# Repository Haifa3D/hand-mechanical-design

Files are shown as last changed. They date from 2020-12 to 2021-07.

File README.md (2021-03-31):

# Oded Hand Mechanical Design  

This project is a sub-project of Haifa3D Robotic Hand.
In this project, we present the mechanical design of the Oded Hand – a 3D printed robotic hand with five micro-DC motors. 
The aim of this design is to be low cost, accessible, easy to assemble, robust and lightweight.  

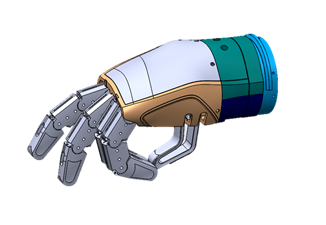
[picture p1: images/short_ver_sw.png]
diagram
   hand_gif  

## Design Description  
The Oded Hand can perform a variety of user-defined hand configurations using an autonomous adaptive grip along with a variety of grip force levels.
The mechanical design consists of four fingers with four different tendon-driven mechanisms actuated by four different micro-DC motors, a passive thumb with two discrete positions using two magnets and wrist rotation driven by planetary gears and a DC motor. 
Each finger is an independent module, hence from a developer point-of-view, you can check new finger designs and change the number of fingers in your hand model. For more details, see the [project presentation](docs/project_presentation.pdf)
All five independent micro-DC motors are driven by a microcontroller system which measures the motors’ current state (see our [Electronic Design](https://github.com/Haifa3D/hand-electronic-design)) and communicate via Bluetooth with additional sensors or systems (see our [Mobile App](https://github.com/Haifa3D/haifa3d-hand-app)).  

## Who can benefit from this Design?  
The design is suitable for users with a below elbow amputation.
We welcome any new developers to enhance our design or to use the Oded Hand as a simulator for your new sensors/algorithms/methods that would potentially help users to control their prosthetic hand.

## Design Files and Versions  
See our detailed [Manual](docs/manual_05dec20.pdf), including printing parameters, assembly instruction and images. *Notice: some of the images are from our previous version but the current version assembly and functionality can be deduced easily according to the same instructions.*
The STL files can be found [here](stl_files) as a folder or [here](stl_files.zip) as a zip file ready to download. The source files (SolidWorks2020) can be sent upon request, while the Parasolid parts can be found [here](xt_files).

## Getting Started:
To build the Oded Hand you will need a basic knowledge of 3D-printing and an access to a 3D printer. 

We use the UP mini 2 printer + ABS / SnapMaker2 + PLA

* Please refer to the [user manual](docs/manual_05dec20.pdf) **before printing** the files for printing parameters, recommendation and more.

* Please download all STL files ([folder](stl_files) or as a [zip file](stl_files.zip)).

* Oded Hand parts list:

| Part Name | Quantity | Hand Module | Right/Left Hand
| --- | --- | --- | --- |
| Gear Finger	| 3x4	 |Finger| Both |
| Gear Finger NR	| 1x4	 |Finger| Both |
| Proximal Phalange	| 1x4	 |Finger| Both |
| Middle Phalange	| 1x4	 |Finger| Both |
| Distal Phalange	| 1x4	 |Finger| Both |
| Pinion D* (or Pinion)	| 1x4	 |Finger Driver| Both |
| Pulley Clip	| 1x4	 |Finger Driver| Both |
| Finger Motor Chassis	| 1x4	 |Finger Driver| Both |
| Single Pulley	| 1x4	 |Finger Driver| Both |
| Palm Cover	| 1	 |Palm| Right** |
| Palm	| 1	 |Palm| Right** |
| Finger module holder	| 1	 |Palm| Right** |
| Thumb	| 1	 |Palm| Right** |
| Planetary Gear	| 3	 |Wrist| Both |
| Wrist Pinion D* (or Wrist Pinion)	| 1	 |Wrist| Both |
| Rotator Housing	| 1	 |Wrist| Right** |
| Rotator Upper Adaptor	| 1	 |Wrist| Right** | 
| Rotator Lower Adaptor	| 1	 |Wrist| Right** |
| Rotator Base	| 1	 |Wrist| Both |
| Wrist Cover	| 1	 |Wrist| Both |

\* D-shape is preferable. 
\** Parts need to be mirrored for left hand model. 

* tools and materials list

  **tools:**
  1. Nippers
  2. Soldering iron and solder
  3. Flat file
  4. Drill (optional)
  
  **Materials:**
  1.	Common Filament (Ø1.75 [mm])
  2.	Thick filament (Ø2.85 [mm])
  3.	Nylon thread 0.6 diameter[mm]
  4.	Silicon tube (outer diameter 8 [mm])
  5.	1 Stainless Steel Rod Ø4x30 [mm] (length 29-34[mm] are also optional)
  6.	2 Magnet N52 Ø6x4
  7.	5 Hex headless screw M3x4 or M3x5
  8.	1 Machined Screw and nut M2x8 [mm] (length 8-10[mm] are also optional)
  9.	6 self-tap Screws M2x8
  10.	2 Machine screws and nuts M3x40 [mm]
  11.	Electrical Wire for ~0.5 [amp]
  12.	5 micro metal gear motors – N20 dc motor, 6V, LP or MP (low or middle power), between 100-200 RPM for the fingers (we are using 200 RPM) and 30 RPM for the wrist. For instance, an [aliexpress seller](https://www.aliexpress.com/item/4000274747864.html?spm=a2g0s.9042311.0.0.64f14c4dRZbTvU).

After you complete the mechanical assembly of the Oded Hand according to the [Manual](docs/manual_05dec20.pdf), please refer to the [Electronic Design](https://github.com/Haifa3D/hand-electronic-design) to assemble the PCB. If you have already assembled the mechanical and the electrical parts, you are welcome to check out our [Mobile App](https://github.com/Haifa3D/haifa3d-hand-app) to refine the controller parameters and to define your favorite hand movements.

## Acknowledgements:
This project was done by a group of great people and with the help and guidance of generous organizations.

*Mechanical design*:  Oded Katzman, Shunit Polinsky, Frank Schenk, Avital Dellariccia, SU-PAD company and Taga Product Design Company, Israel.

*Users Communication*: Haifa 3D – a nonprofit organization that designs and builds hands for free, founded by Yoav Medan and Yacov Malinovich.

*Resources*: The Technion - Israel Institute of Technology and special thanks to Prof. Alon Wolf and the Biorobotics and Biomechanics Lab.

## Donation:


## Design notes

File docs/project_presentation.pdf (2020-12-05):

# Design for a Low-Cost 3D Printed Electro-Mechanical Prosthetic Hand

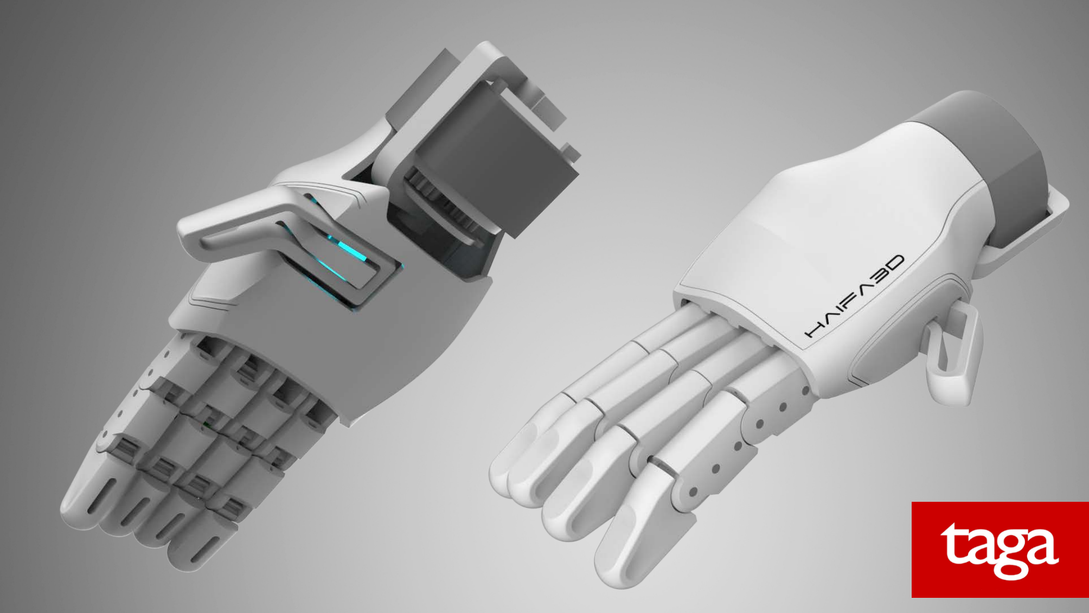
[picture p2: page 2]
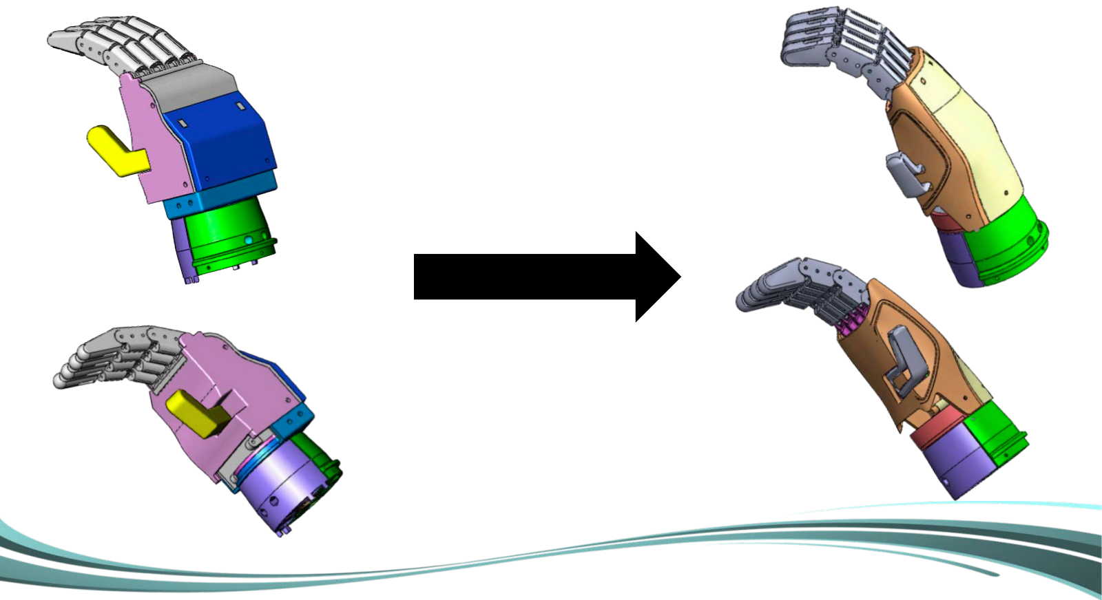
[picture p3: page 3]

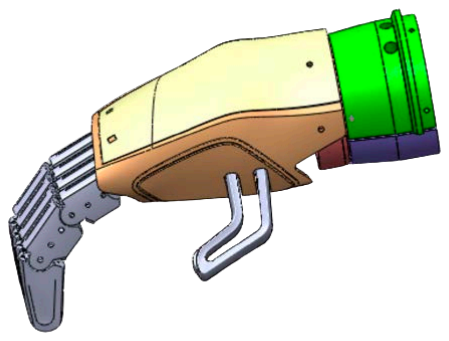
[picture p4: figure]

## - Low cost - Accessible - 3D printed - Easy to assemble - Off-the-shelf components - Open source - Robust and light

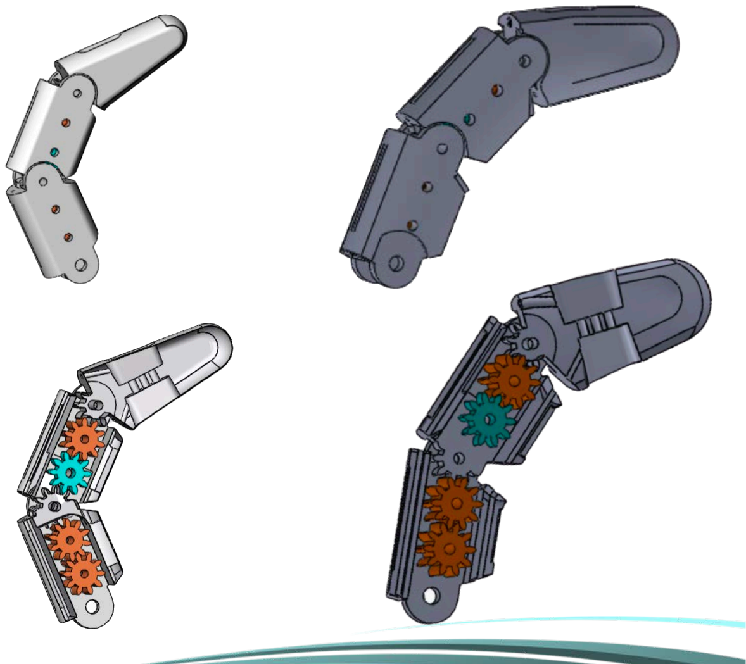
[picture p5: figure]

# Fingers

Modifications:
- more human-like shape
- Curved surfaces

Main features:
- fully actuated (1 DoF for each actuator)
- Similar path length for inner and outer cable

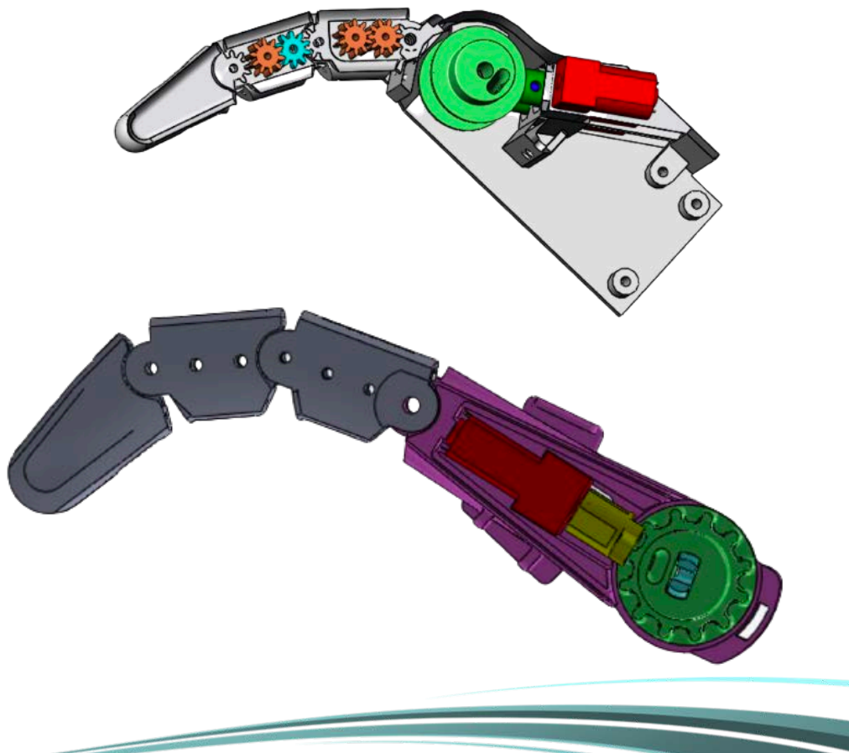
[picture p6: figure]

# Finger module

Modifications:
- Main difference from previous design
- Allows a smoother and more natural profile of the hand
- Each finger and its mechanism is an independent element

Main features:
DC motor connected to pinion rotates pulley that pulls cables connected to phalanges

# Finger module

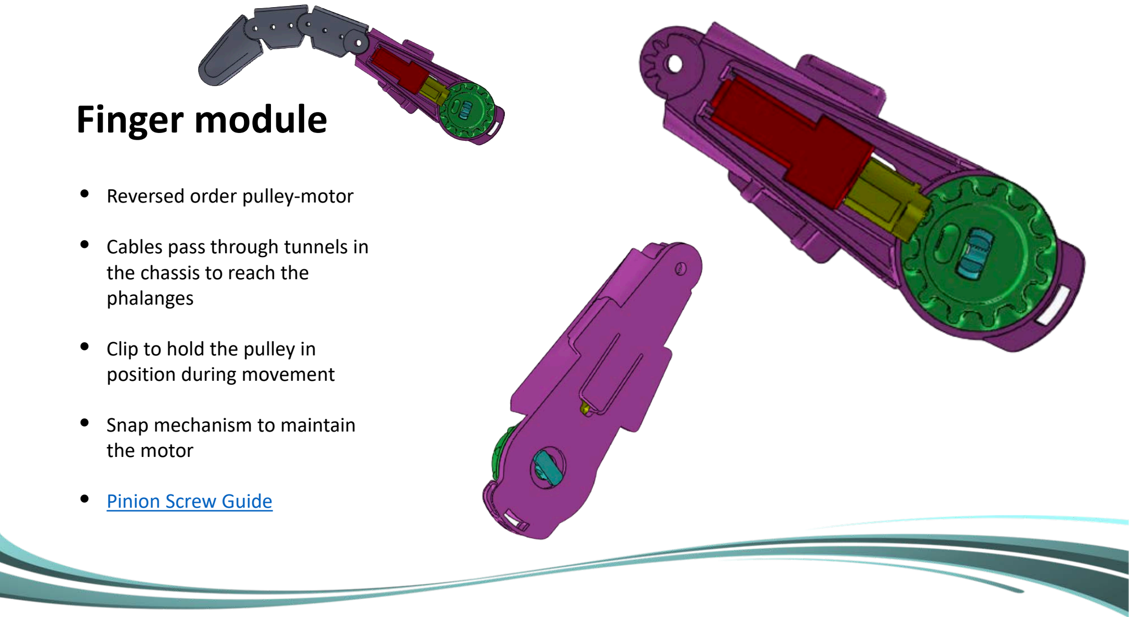
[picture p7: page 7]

- Reversed order pulley-motor
- Cables pass through tunnels in the chassis to reach the
phalanges
- Clip to hold the pulley in position during movement
- Snap mechanism to maintain the motor
- Pinion Screw Guide

Pinion Screw Guide | Pinion

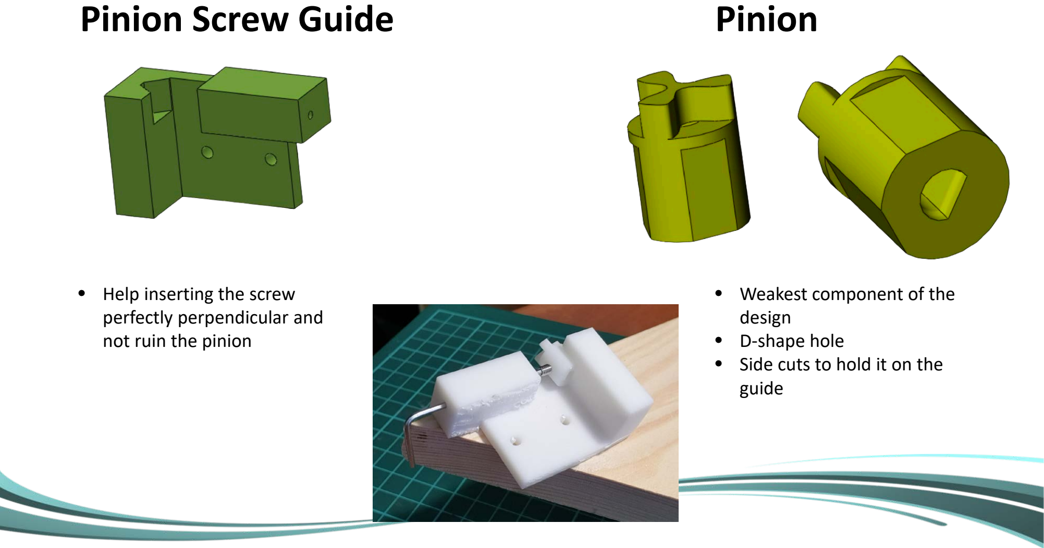
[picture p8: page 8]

- Weakest component of the design
- D-shape hole
- Side cuts to hold it on the guide
- Help inserting the screw perfectly perpendicular and not ruin the pinion

# Palm

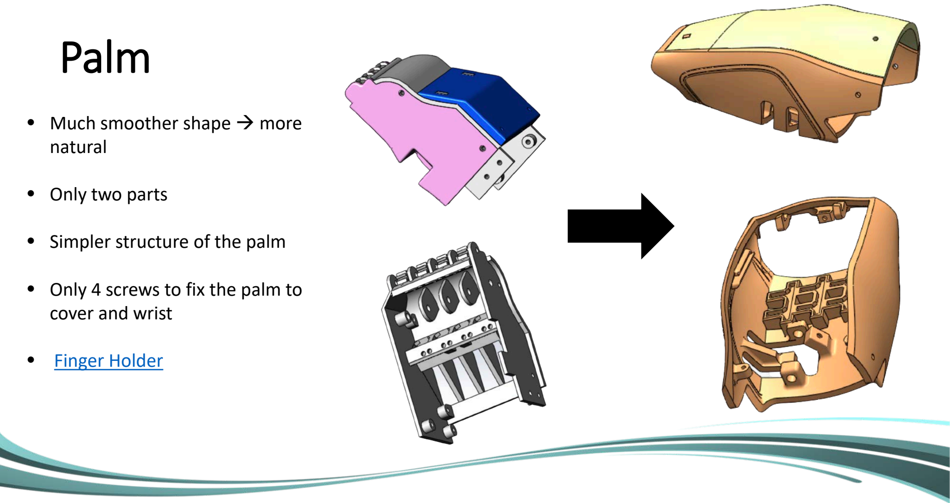
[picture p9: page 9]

- Much smoother shape → more natural
- Only two parts
- Simpler structure of the palm
- Only 4 screws to fix the palm to cover and wrist
- Finger Holder

# Finger Holder

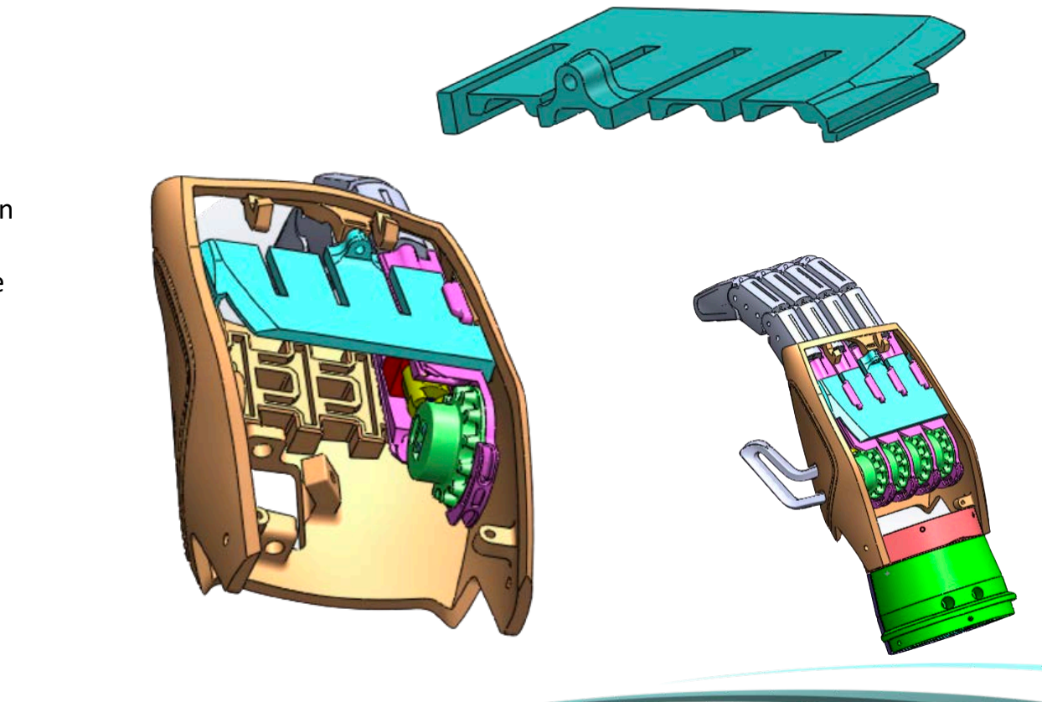
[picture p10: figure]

- Finger holder and pattern on the bottom of the palm,
allow to save space because there is no need for a
complicated structure to
hold the fingers’ motor-pulley mechanism
- Finger holder is simply
inserted in tunnels on the side of the palm and
stopped with a machined
screw

# Thumb

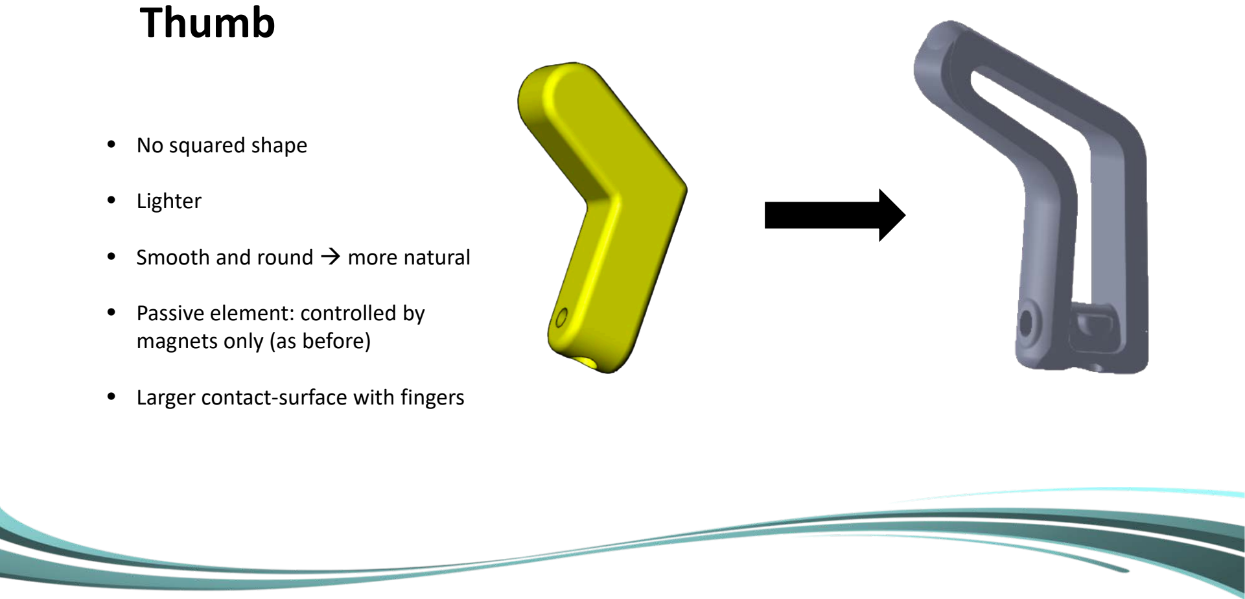
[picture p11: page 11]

- No squared shape
- Lighter
- Smooth and round → more natural
- Passive element: controlled by magnets only (as before)
- Larger contact-surface with fingers

# Thumb

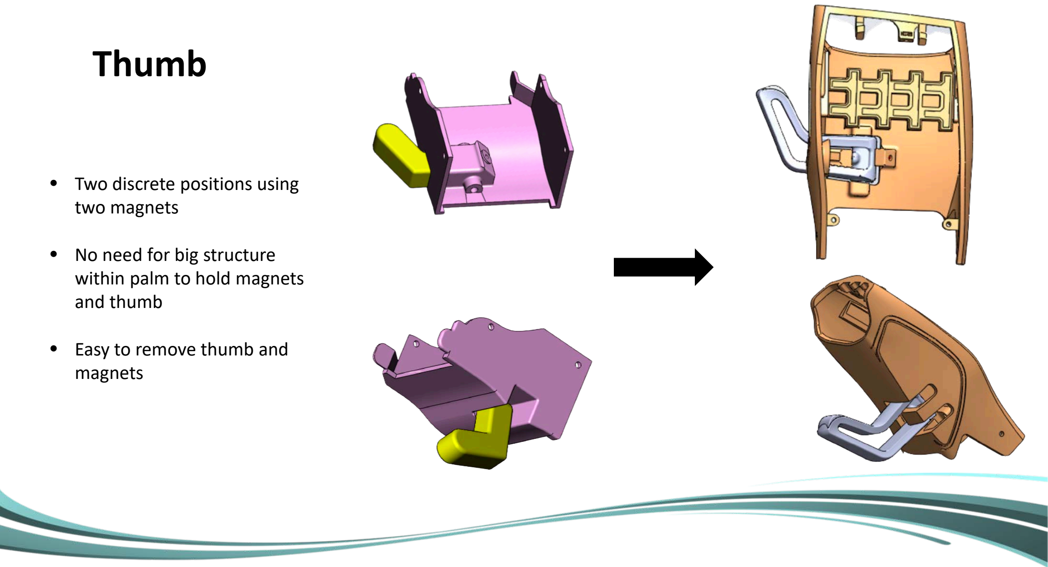
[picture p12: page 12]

- Two discrete positions using two magnets
- No need for big structure within palm to hold magnets and thumb
- Easy to remove thumb and magnets

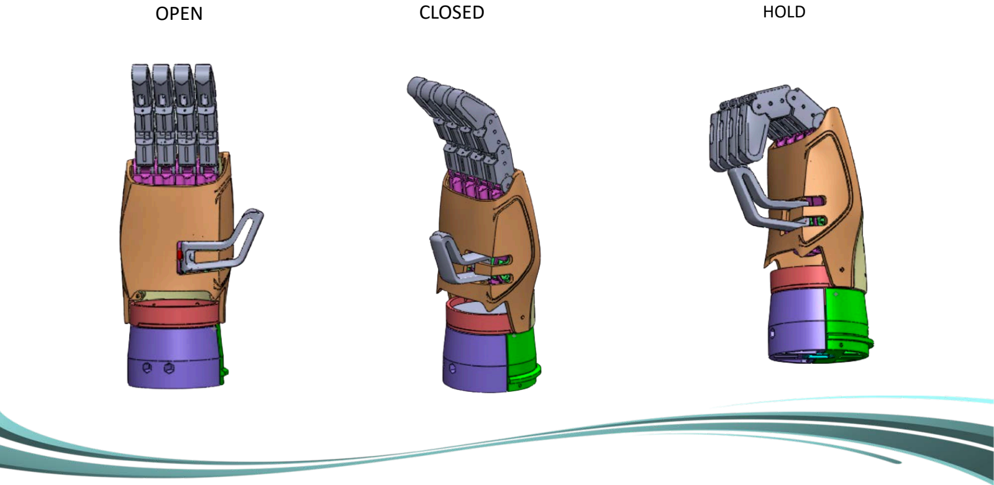
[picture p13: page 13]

OPEN | CLOSED | HOLD

# Wrist

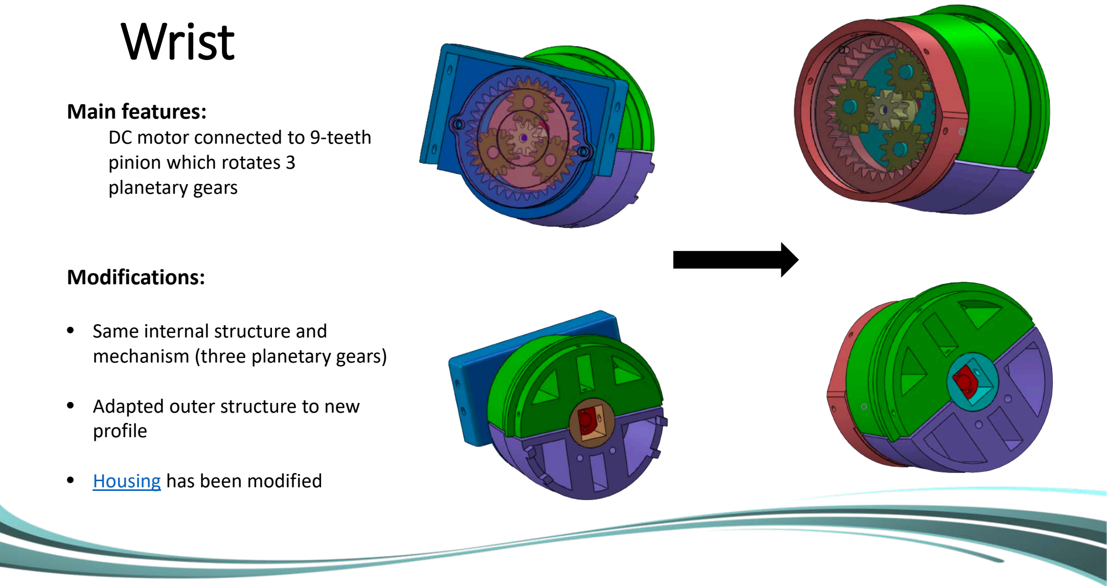
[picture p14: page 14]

Modifications:

- Same internal structure and mechanism (three planetary gears)
- Adapted outer structure to new profile
- Housing has been modified

Main features:
DC motor connected to 9-teeth pinion which rotates 3
planetary gears

## Wrist Housing

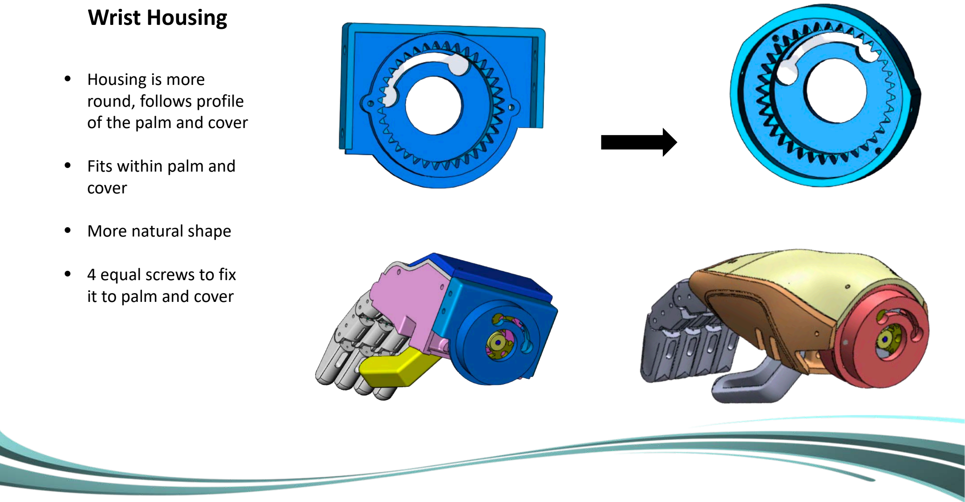
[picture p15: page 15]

- Housing is more
round, follows profile
of the palm and cover
- Fits within palm and
cover
- More natural shape
- 4 equal screws to fix
it to palm and cover

## Testing:

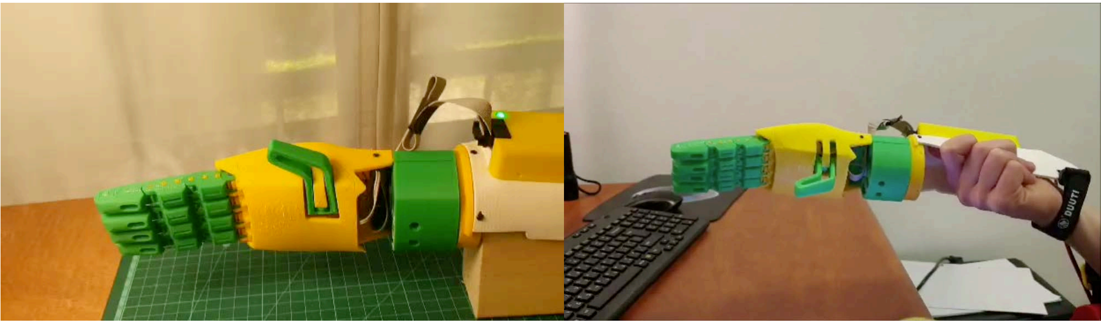
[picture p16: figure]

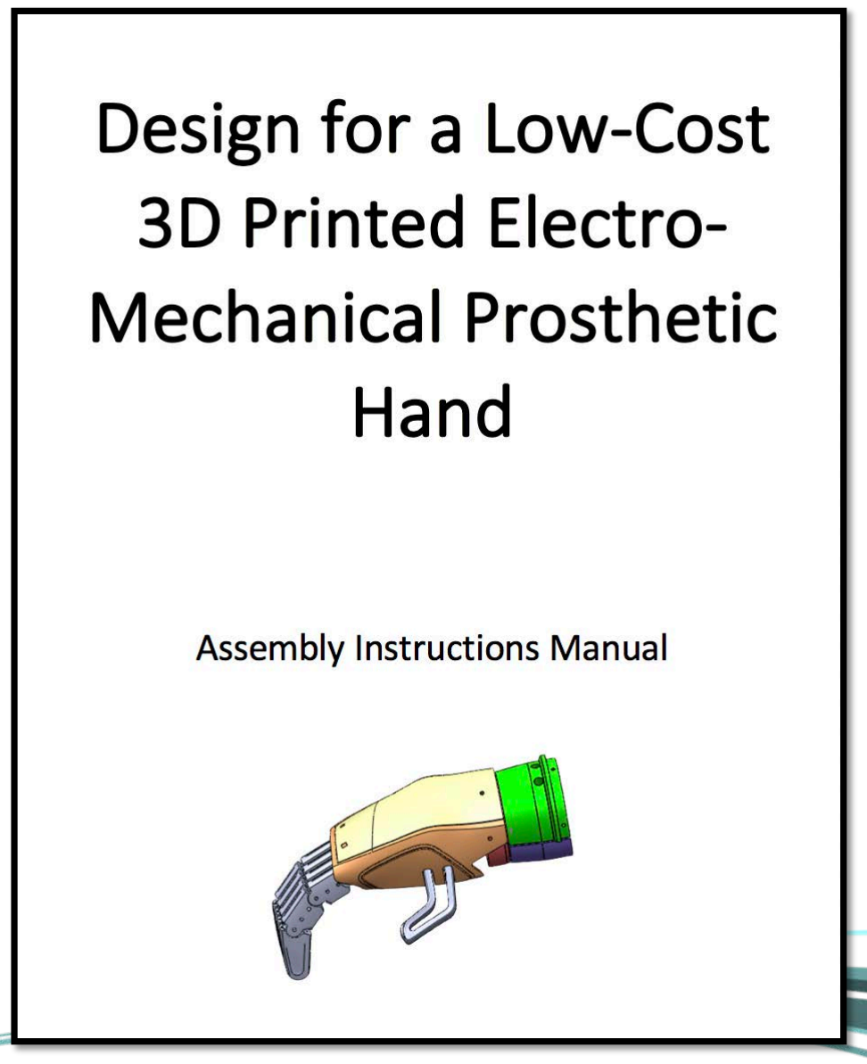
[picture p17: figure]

### Manual:

- Simple to understand
- List of all the materials
- Images of every step
- Guidance for printing orientation
- Printing parameters for every part
- Open source
- Manual

# Future modifications:

## Shortened finger

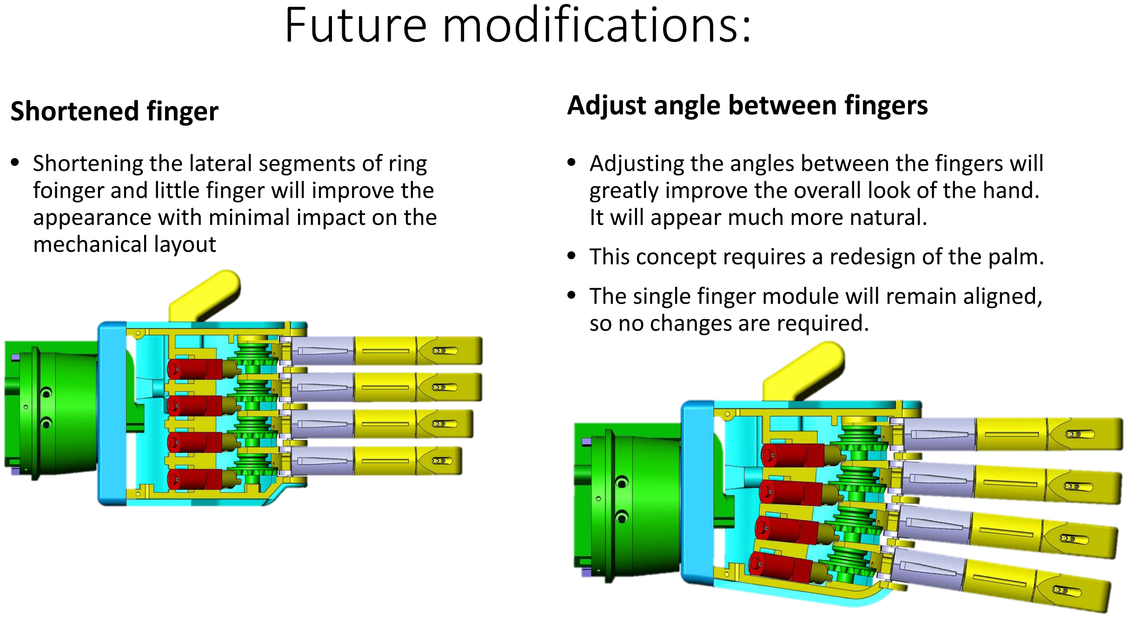
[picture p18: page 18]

- Shortening the lateral segments of ring foinger and little finger will improve the appearance with minimal impact on the mechanical layout

## Adjust angle between fingers

- Adjusting the angles between the fingers will greatly improve the overall look of the hand. It will appear much more natural.
- This concept requires a redesign of the palm.
- The single finger module will remain aligned, so no changes are required.

# Future modifications:

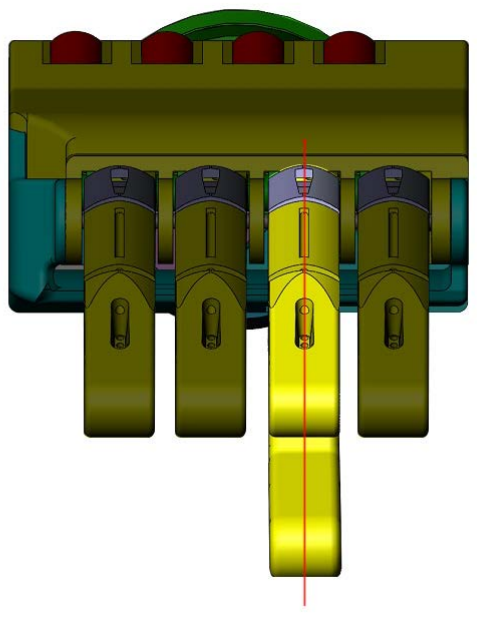
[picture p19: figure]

- Stopping the rotating thumb at
an angle that allows for the index finger to perform the pinch might simplify this operation.
- It appears as though the pinch grab between thumb and middle finger might make it hard to see and aim for the object.

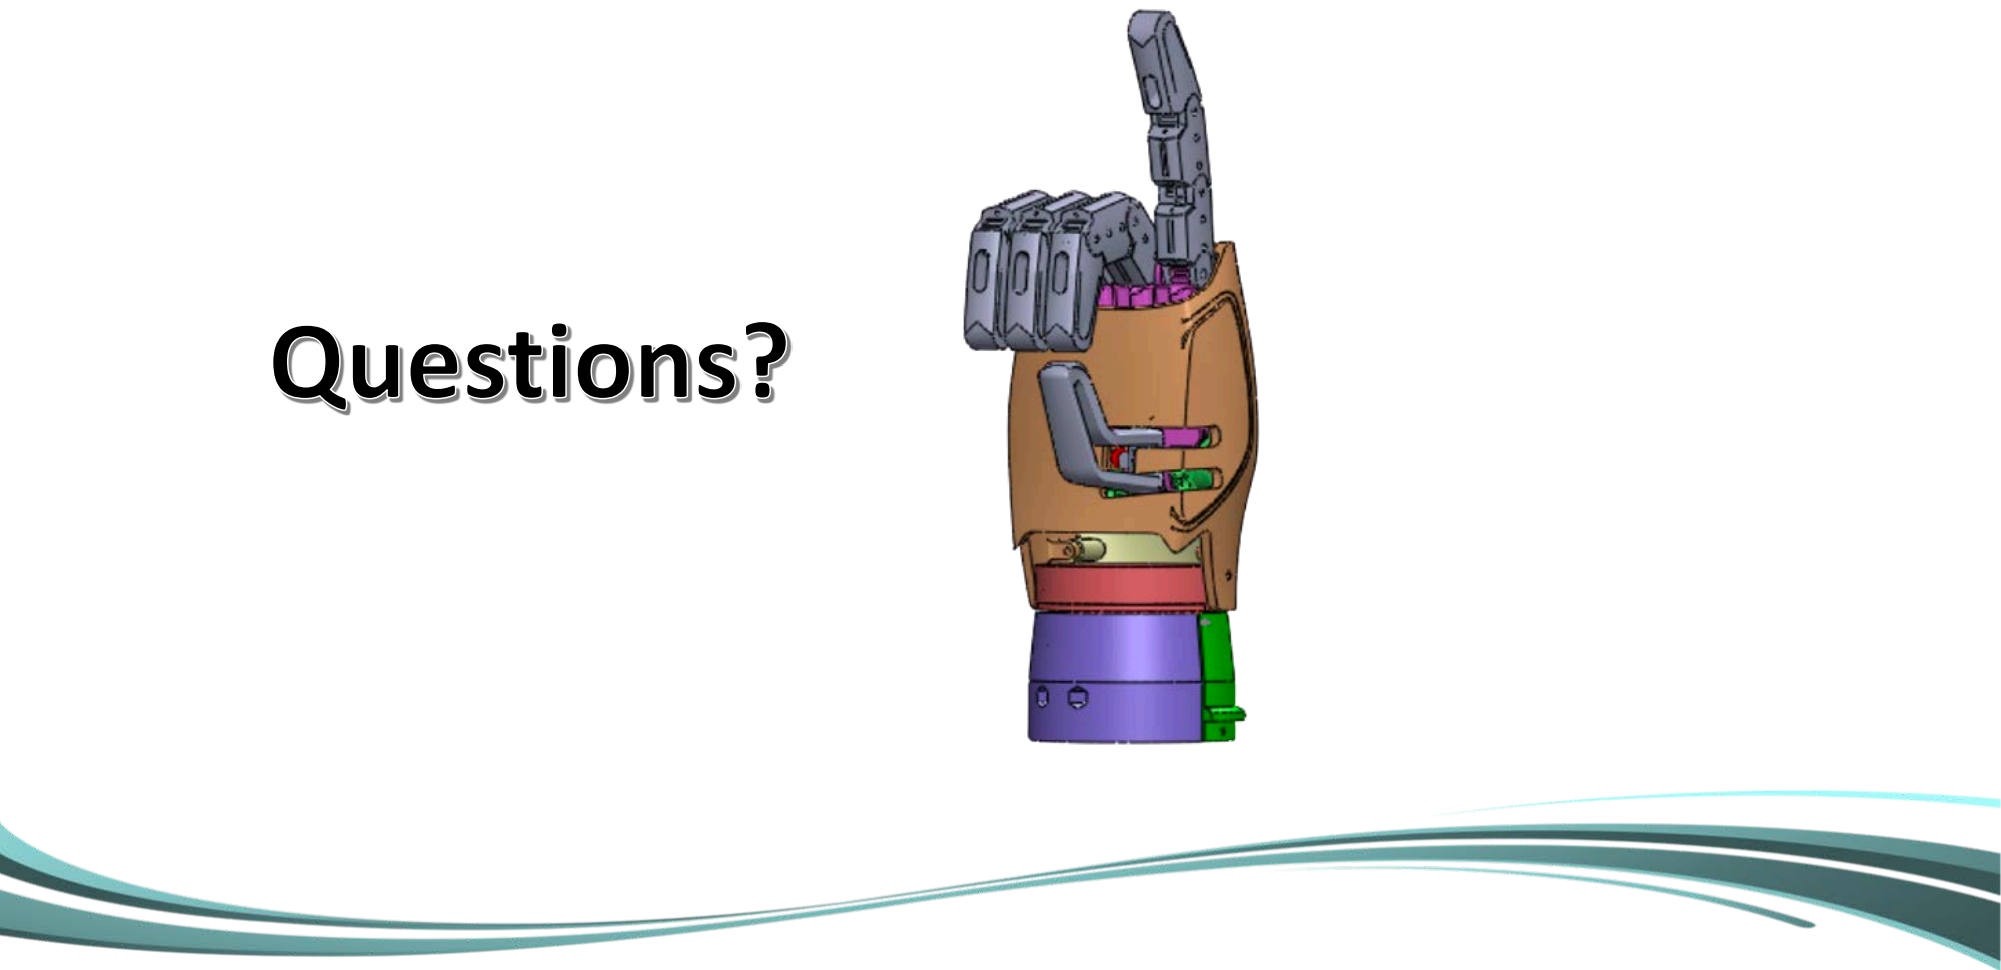
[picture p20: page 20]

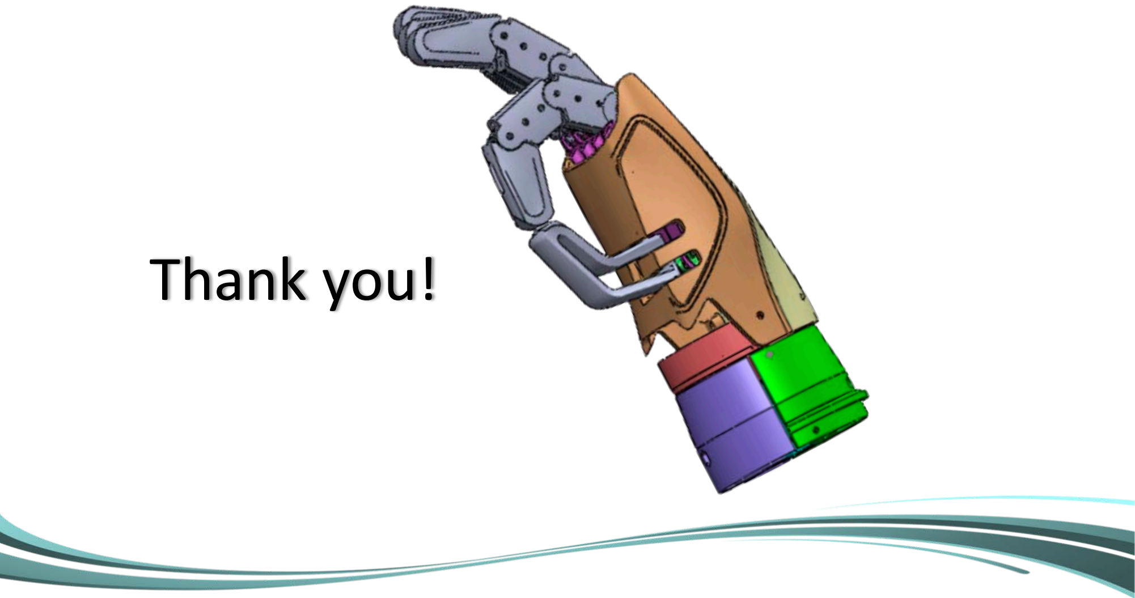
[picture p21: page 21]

# Thank you!

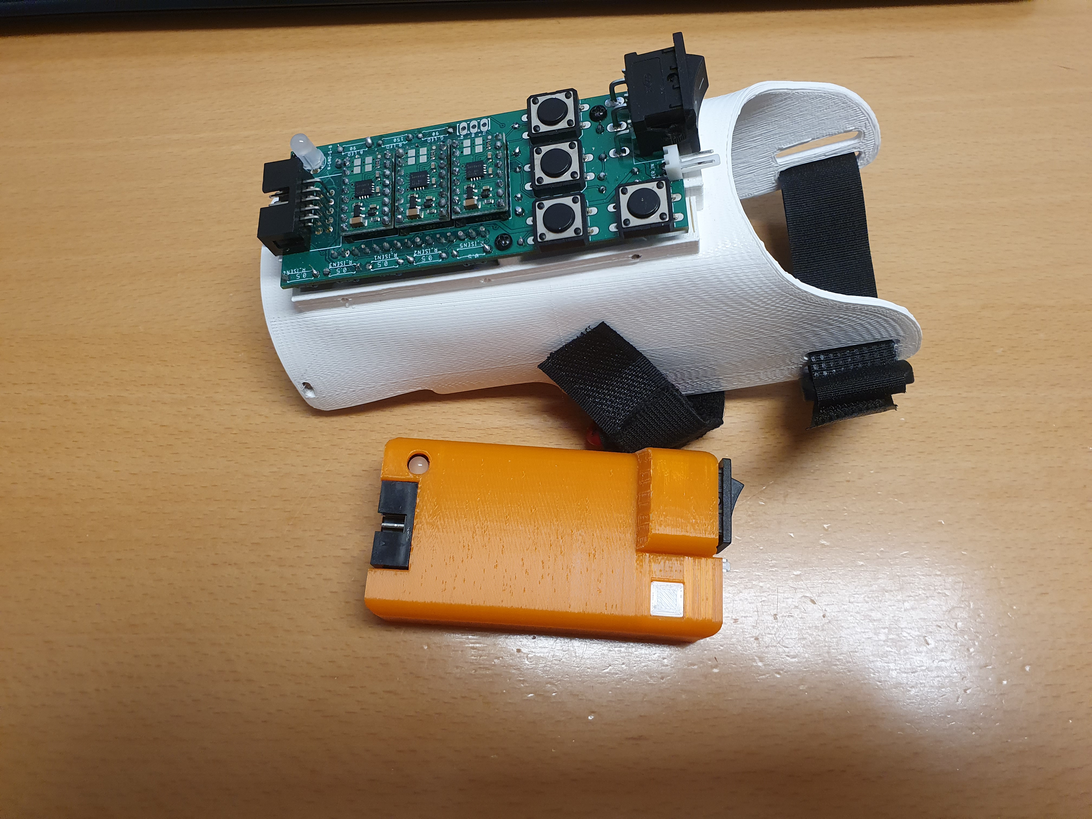
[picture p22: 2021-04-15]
images/electronics.jpg

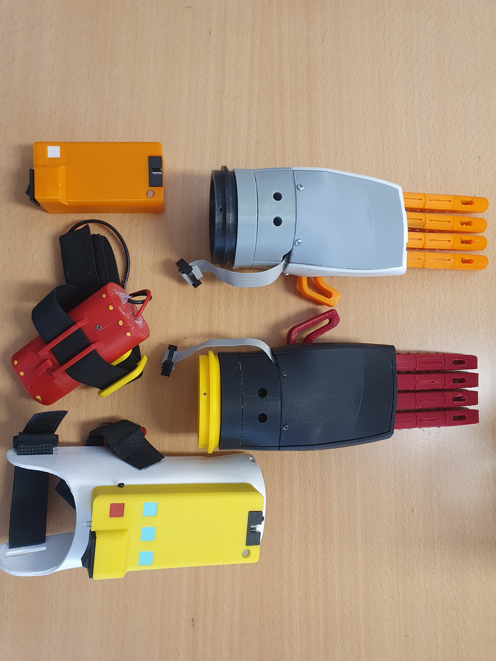
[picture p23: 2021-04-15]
images/all_top.jpg

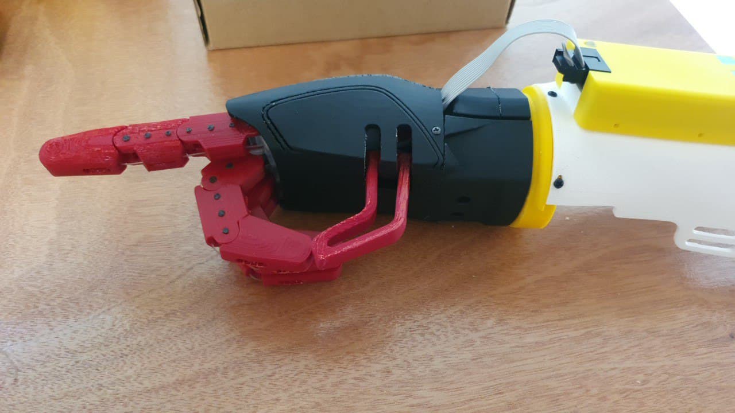
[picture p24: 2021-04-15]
images/right_pointing_side.jpg

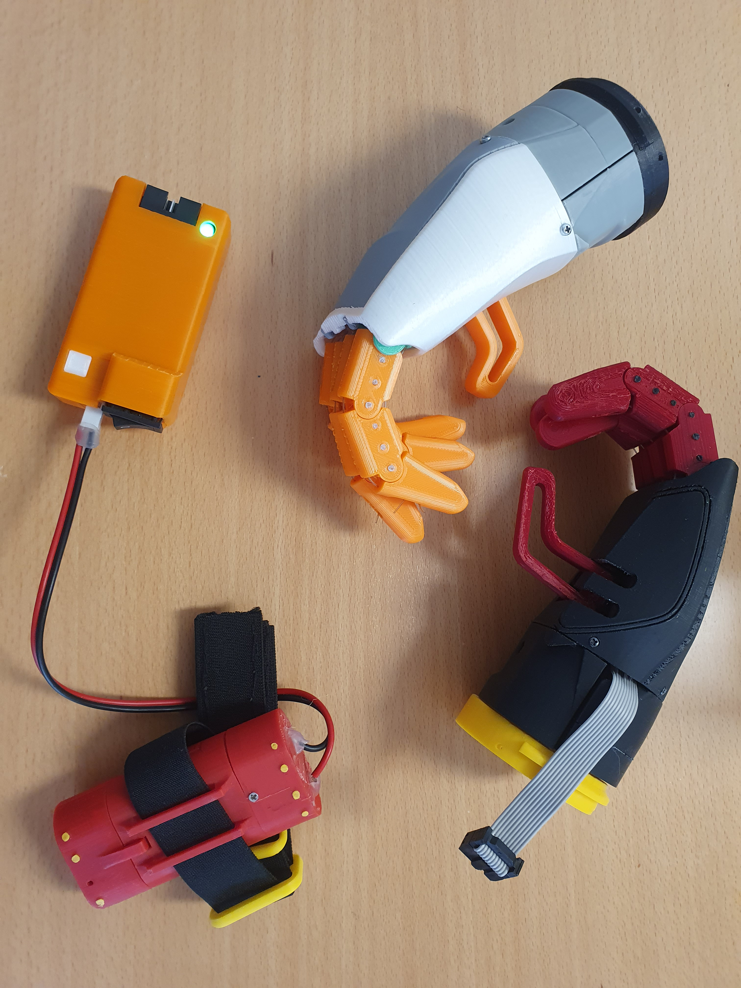
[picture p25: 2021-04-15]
images/all_side.jpg

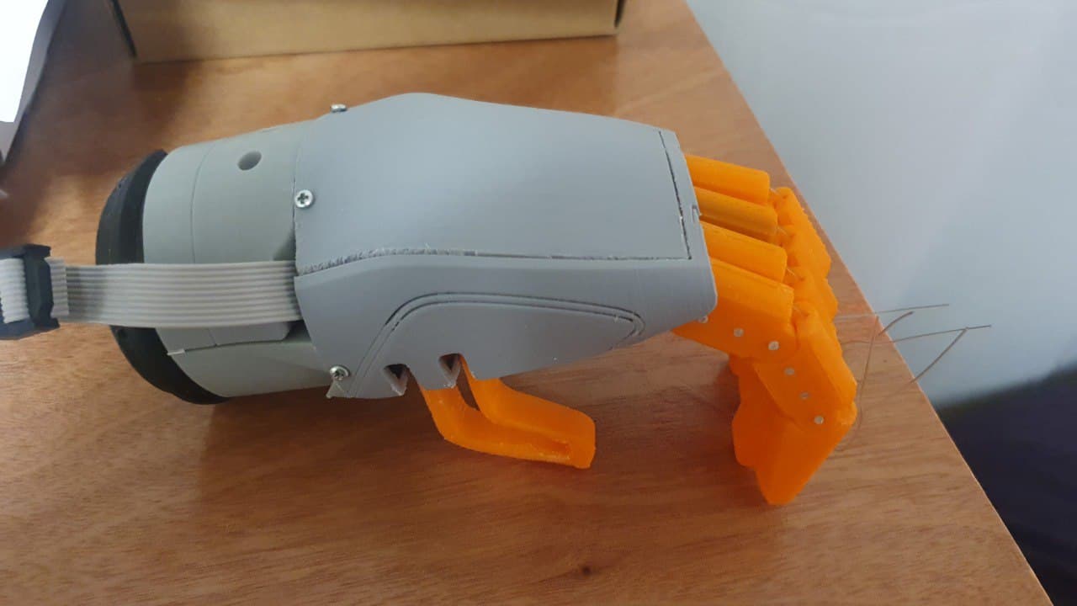
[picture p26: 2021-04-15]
images/left_close_side.jpg

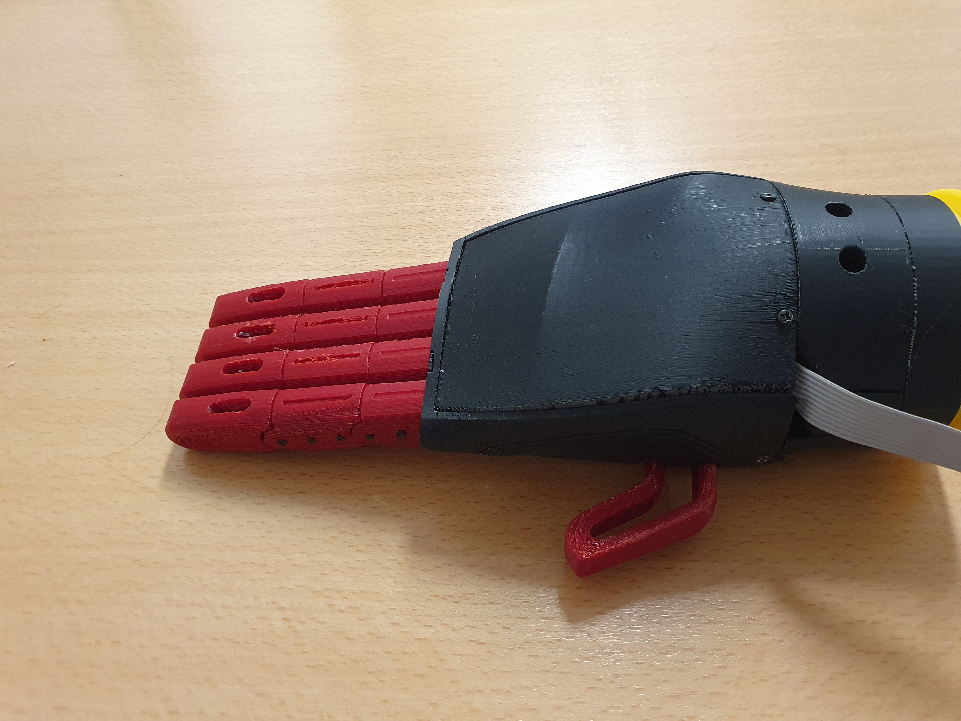
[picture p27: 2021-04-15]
images/right_open_top.jpg

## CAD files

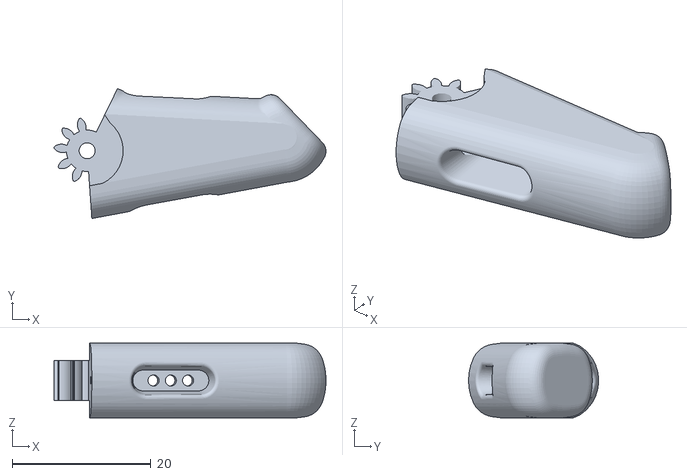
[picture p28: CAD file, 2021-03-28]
stl_files/stl_files_left/Finger Module/Distal phalange.STL
39.2 x 18.8 x 10.8

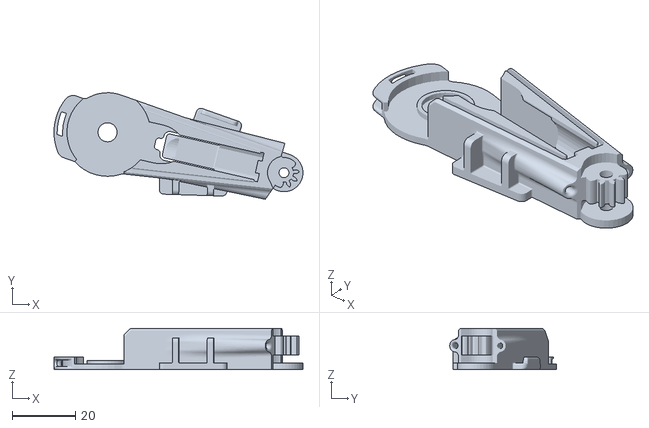
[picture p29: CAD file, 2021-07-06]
stl_files/stl_files_left/Finger Module/human-like-fingers/Finger motor chassis LEFT HL.STL
78.5 x 33.6 x 13.0

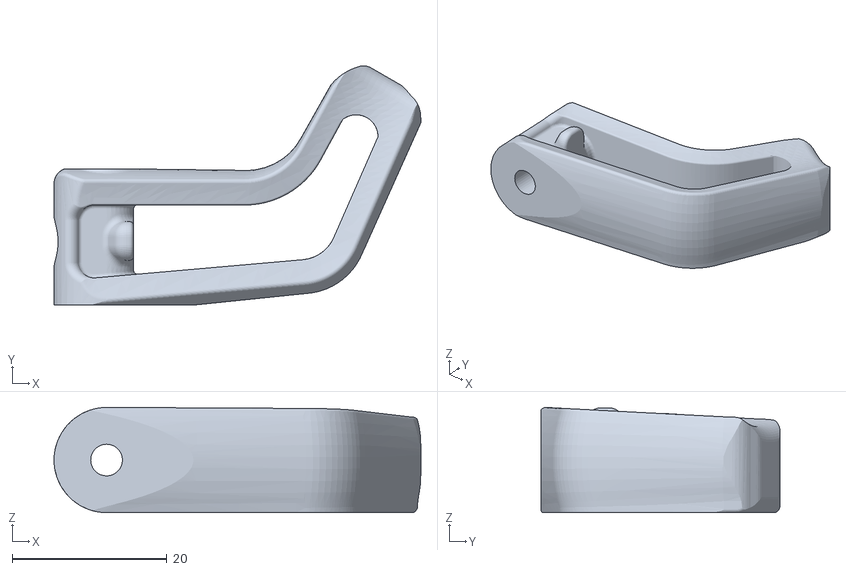
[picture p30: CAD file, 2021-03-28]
stl_files/stl_files_left/Palm/Thumb LEFT.STL
47.5 x 30.9 x 13.6

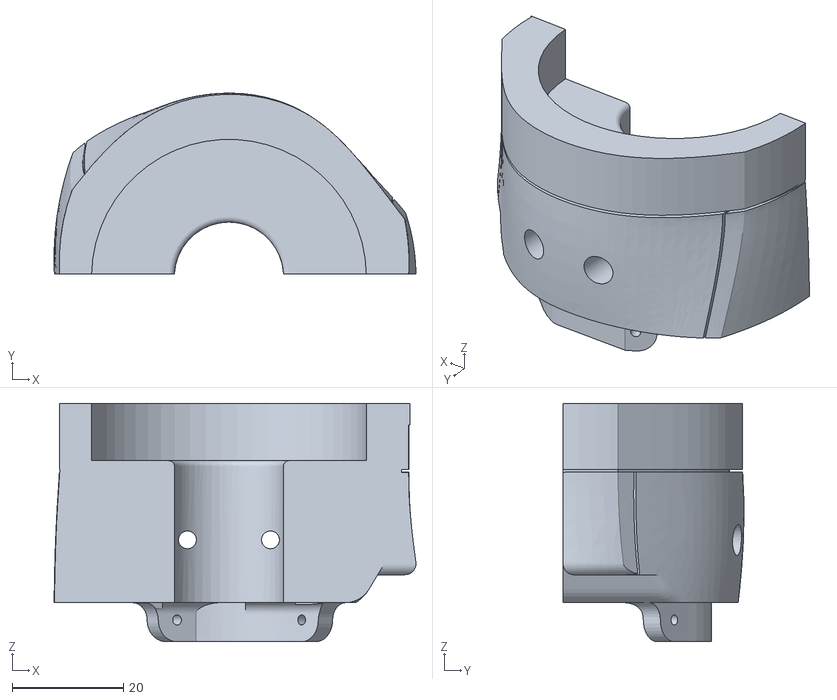
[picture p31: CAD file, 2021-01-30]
stl_files/stl_files_left/Wrist/Rotator Upper Adaptor LEFT.STL
64.9 x 32.5 x 42.8

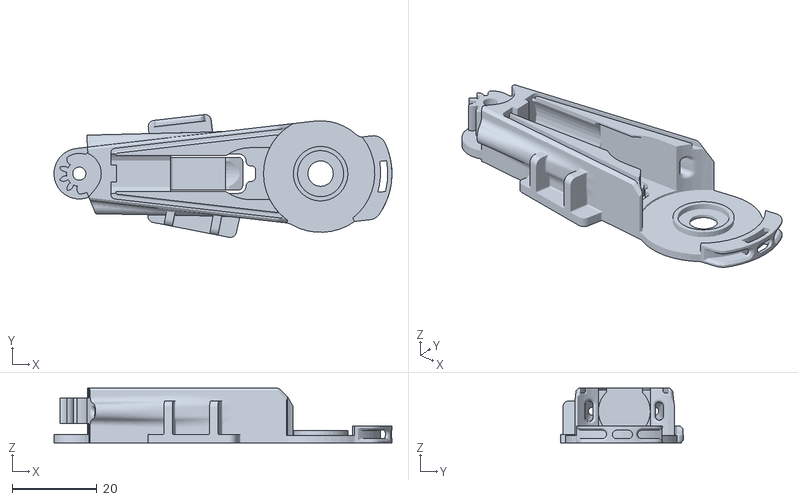
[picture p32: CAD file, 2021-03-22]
stl_files/stl_files_right/Finger Module/human-like-fingers/Finger motor chassis RIGHT HL.STL
79.9 x 29.0 x 13.0

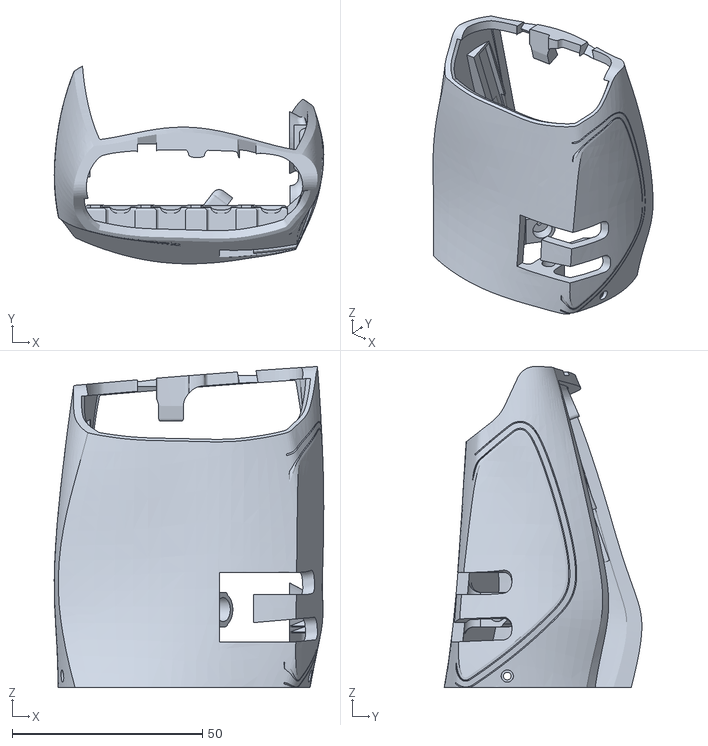
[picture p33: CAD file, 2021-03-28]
stl_files/stl_files_right/Palm/Palm RIGHT.STL
70.7 x 51.9 x 84.3

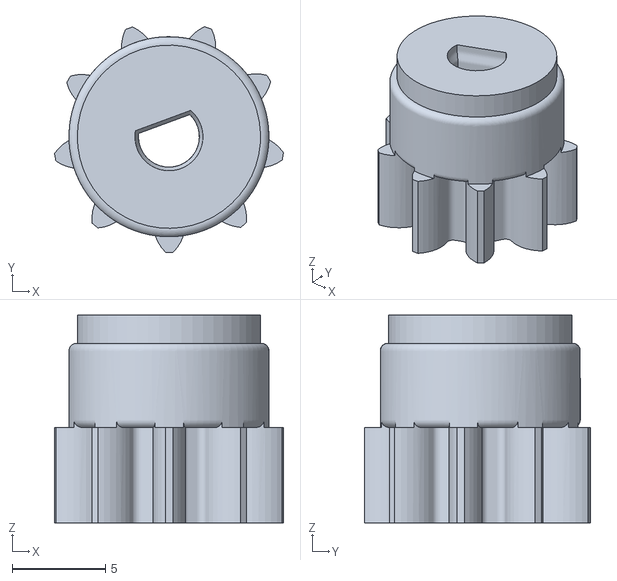
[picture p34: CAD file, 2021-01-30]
stl_files/stl_files_right/Wrist/Wrist Pinion D.STL
12.2 x 12.1 x 11.1

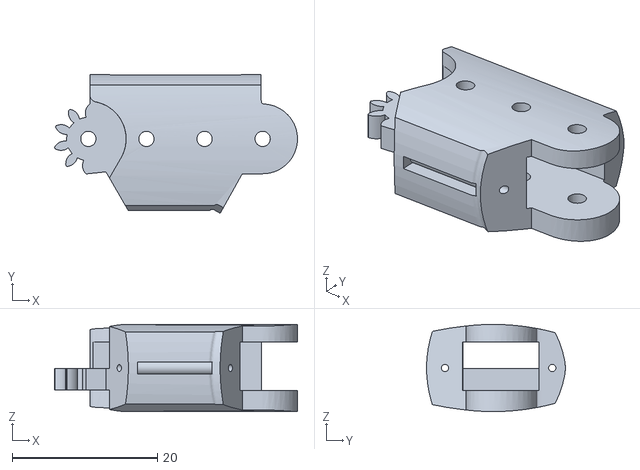
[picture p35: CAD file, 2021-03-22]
stl_files/stl_files_left/Finger Module/human-like-fingers/Middle phalange HL.STL
33.5 x 19.1 x 12.0

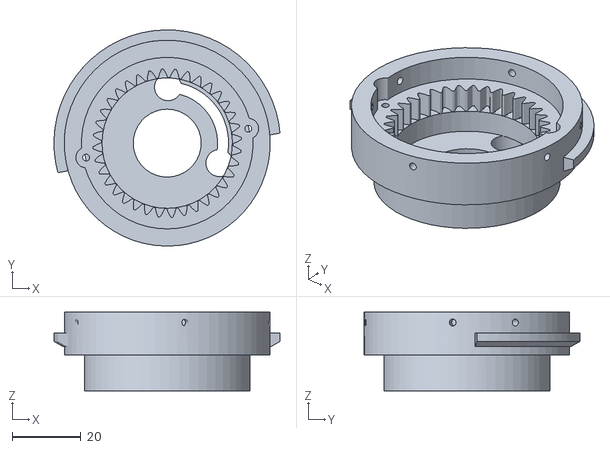
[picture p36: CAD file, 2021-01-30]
stl_files/stl_files_left/Wrist/Rotator Housing LEFT.STL
65.9 x 63.0 x 22.9

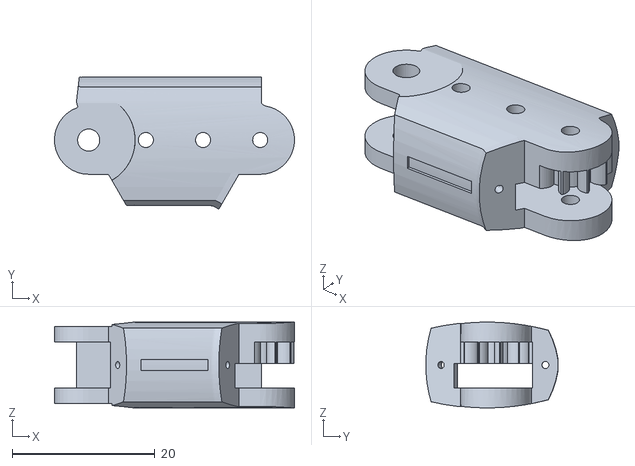
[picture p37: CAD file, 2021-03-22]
stl_files/stl_files_right/Finger Module/human-like-fingers/Proximal phalange HL.STL
33.6 x 18.5 x 12.0

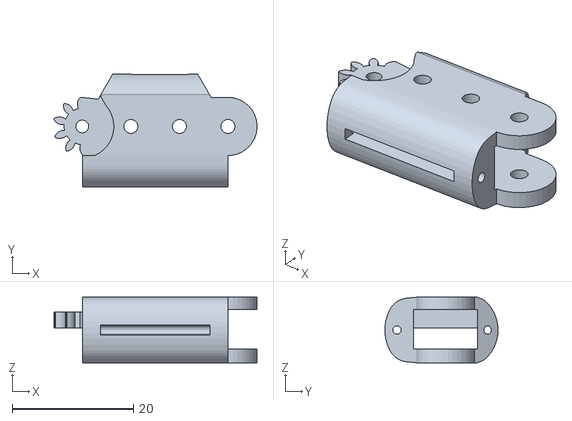
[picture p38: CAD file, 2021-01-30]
stl_files/stl_files_right/Finger Module/Middle phalange.STL
33.4 x 18.6 x 10.8

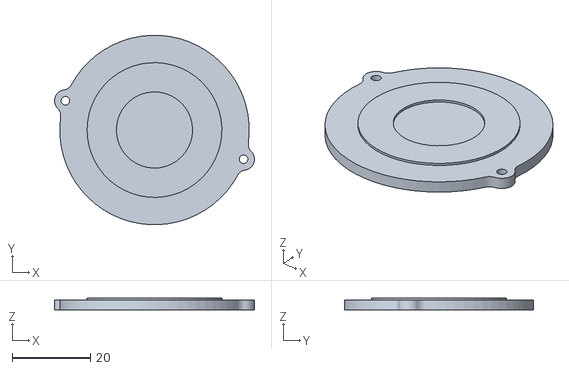
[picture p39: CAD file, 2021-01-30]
stl_files/stl_files_right/Wrist/Wrist Cover.STL
51.2 x 48.5 x 3.00

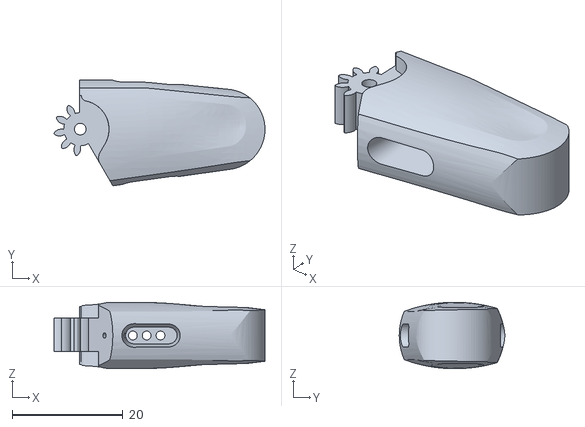
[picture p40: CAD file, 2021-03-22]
stl_files/stl_files_left/Finger Module/human-like-fingers/Distal phalange HL.STL
38.1 x 19.1 x 12.0

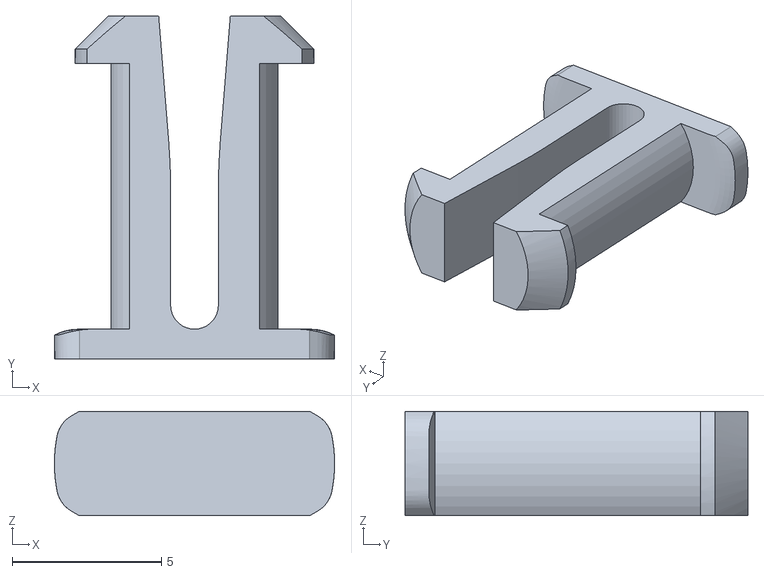
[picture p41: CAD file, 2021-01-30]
stl_files/stl_files_left/Finger Module/Pulley clip.STL
9.40 x 11.5 x 3.50

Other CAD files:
stl_files/stl_files_left/Finger Module/Finger motor chassis LEFT.STL
stl_files/stl_files_left/Palm/Palm LEFT.STL
stl_files/stl_files_right/Palm/Thumb RIGHT.STL
stl_files/pinion screw guide.STL
stl_files/stl_files_left/Finger Module/Finger Gear NR.STL
stl_files/stl_files_left/Finger Module/Finger Gear.STL
stl_files/stl_files_left/Finger Module/Middle phalange.STL
stl_files/stl_files_left/Finger Module/Pinion D loose.STL
stl_files/stl_files_left/Finger Module/Pinion D.STL
stl_files/stl_files_left/Finger Module/Pinion.STL
stl_files/stl_files_left/Finger Module/Proximal phalange.STL
stl_files/stl_files_left/Finger Module/Single Pulley.STL
stl_files/stl_files_left/Palm/Finger module holder LEFT.STL
stl_files/stl_files_left/Palm/Palm Cover LEFT.STL
stl_files/stl_files_left/Wrist/Planetary Gear.STL
stl_files/stl_files_left/Wrist/Rotator Base.STL
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
